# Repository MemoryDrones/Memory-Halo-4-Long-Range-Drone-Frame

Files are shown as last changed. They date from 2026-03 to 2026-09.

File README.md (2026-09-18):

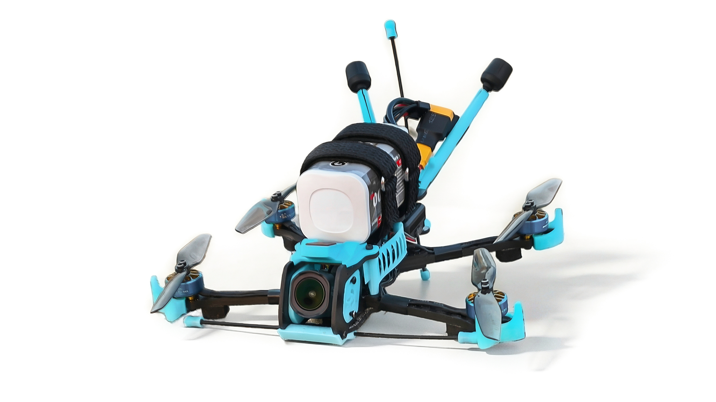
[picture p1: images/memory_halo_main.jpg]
Memory Halo 4 Frame


# Memory Halo 4 Long Range Drone Frame

An open source 4 inch long range FPV drone, designed for those that prefer a stronger frame with less vibrations and no jello. This repository includes DXF carbon cutting files for CNC fabrication and STL files for 3D prints aswell as the hardware and documentation needed for one frame. 

## Features

- 4" Propellor size
- Deadcat configuration
- 0-30 Degree camera angle, nothing obstructs the view, but the camera stays 100% protected!
- Plenty of room inside to fit everything (buzzer, capacitor,...)
- Stack mounting: 20x20mm M3 / 25.5x25.5mm M2 / 25.5x25.5mm M2 (angled 45°)
- Vtx mounting: 20x20mm M2 / 25.5x25.5mm M2
- Motor mounting: 9x9mm and 12x12mm
- Camera support: 19/20mm: Analog, Walksnail, DJI O3 Pro, O4, O4 Pro
- Lightweight: ~205g dry with O4 Pro, ~175g analog
- Supports single or double rear standoff design (seperate middle & top plate design for it)

## Hardware needed
Minimum needed to build the frame. Weight can slightly vary, this is just a guideline.

We have used 20mm standoffs with a diameter of 3.5mm, and a 23mm standoff (for camera plate) with a diameter of 4mm. For any other size, it is possible the TPU files will have to be slightly adjusted.

The frame also uses M2 pressnuts to secure the arms properly in the middle plate.

### Carbon
| Qty | Part name | Details | Weight per piece (g) |
|-----|---|---|---|
| 1 | Bottom plate | Main frame | 5.60 |
| 1 | Middle plate (single standoff or double standoff version) | Main frame | 8.30 / 9.20 |
| 1 | Top plate (single standoff or double standoff version)| Main frame | 8.30 / 9.20 |
| 4 | Arms | Main frame arms | 4.60 |
| 2 | Camera plates | Mounts the camera | 2.10 |

### Standoffs
| Qty | Part name | Details | Weight per piece (g) |
|-----|---|---|---|
| 5 | M2 20mm standoffs | Main spacers | 0.35 |
| 1 | M2 23mm standoff | Spacer for camera plates | 0.40 |

### Screws
| Qty | Part name | Details | Weight per piece (g) |
|-----|---|---|---|
| 4 | M2 14mm screws | Goes through mid plate into standoffs | 0.65 |
| 11 | M2 9mm screws | For everything else | 0.45 |

### Others
| Qty | Part name | Details | Weight per piece (g) |
|-----|---|---|---|
| 4 | M2 pressnuts | Thread inserts for mid plate | 0.45 |
| 2 | Battery pad | Sticky battery pad | 3 |
| 1 | 19/20mm camera mount | TPU camera brackets | 2.2 |

### NOTE: for the "Double rear standoff" version, you need the following extra:
| Qty | Part name | Details | Weight per piece (g) |
|-----|---|---|---|
| 1 | M2 20mm standoffs | Spacer for plate separation | 0.35 |
| 2 | M2 9mm screws | General fasteners | 0.45 |

Total minimum frame weight: ~ 65g

## Repository Content

This repository contains everything needed to cnc cut and build the frame:

- **[/carbon](carbon/)** 
  DXF files for CNC cutting the carbon fiber plates.  
  Includes both **single rear standoff** and **double rear standoff** frame variants (to avoid confusion, please take a look at the readme there).

- **[/3d-prints](3d-prints/)**  
  STL files for TPU printed components such as camera mounts, gps and antenna mounts.

- **[/battery-pad](battery-pad/)**  
  DXF file for laser cutting the battery pad, comes in 2 variations. 

- **[/betaflight-tune](betaflight-tune/)**  
  Betaflight tune specifically for the frame, to get as clean gyro data as possible. indludes screenshots and the cli txt file

- **[/docs](docs/)** 
  Documentation including:
  - Assembly instructions
  [Assembly instructions](docs/assembly-instructions.md)
  - [Example build configurations](docs/build-examples.md)

- **[/images](images/)** 
  Photos and diagrams of the frame are found here.

## Frame assembly

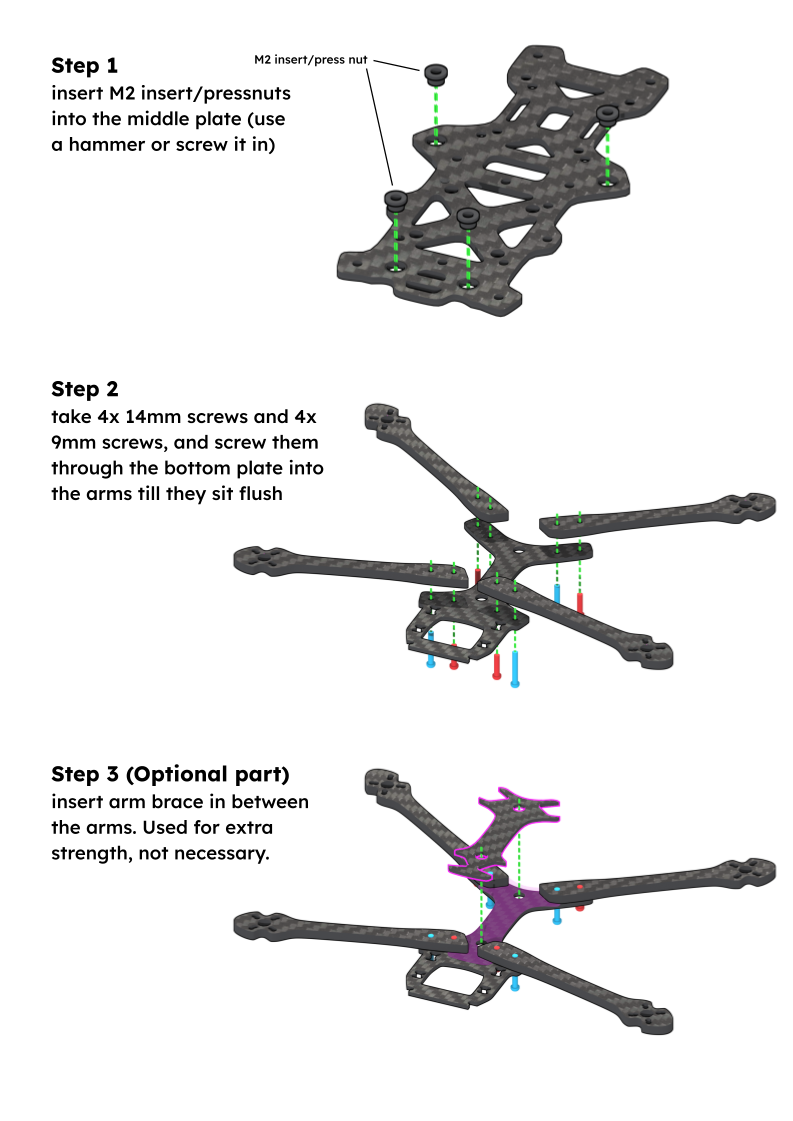
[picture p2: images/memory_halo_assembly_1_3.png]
Memory Halo 4 Frame Assembly Step 1-3


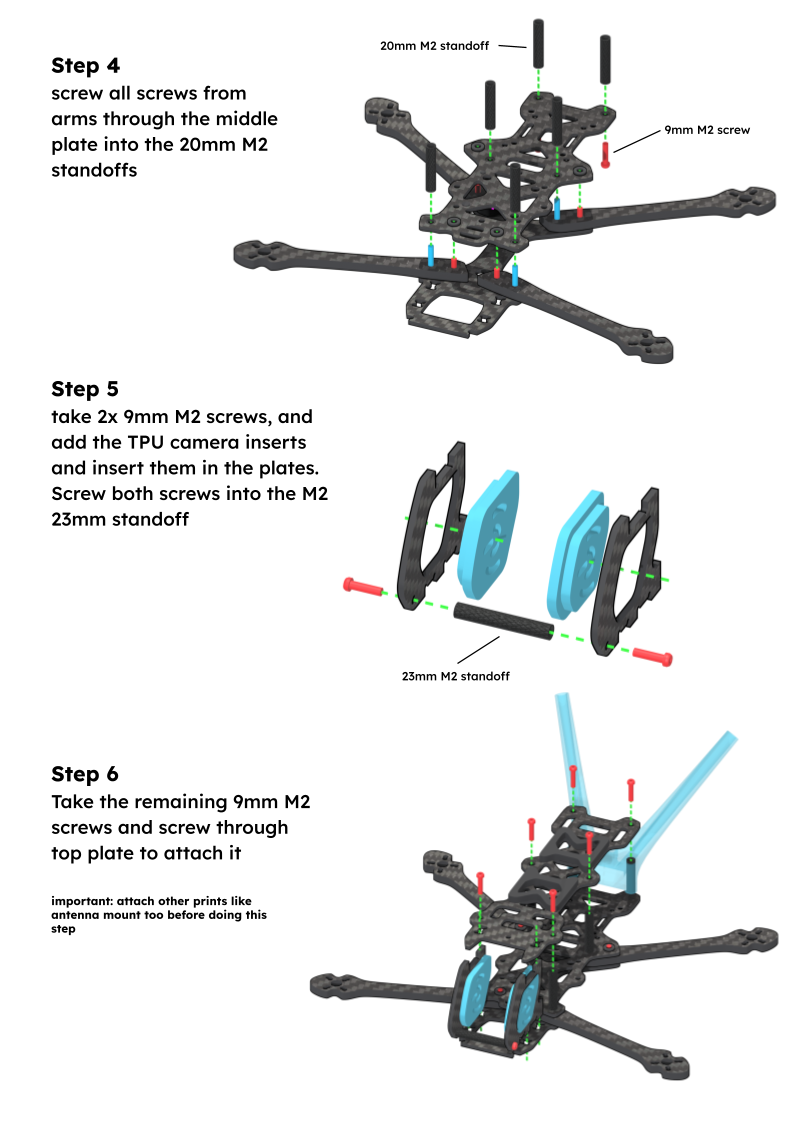
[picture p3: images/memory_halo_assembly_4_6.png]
Memory Halo 4 Frame Assembly Step 4-6


## Photographs of the frame:

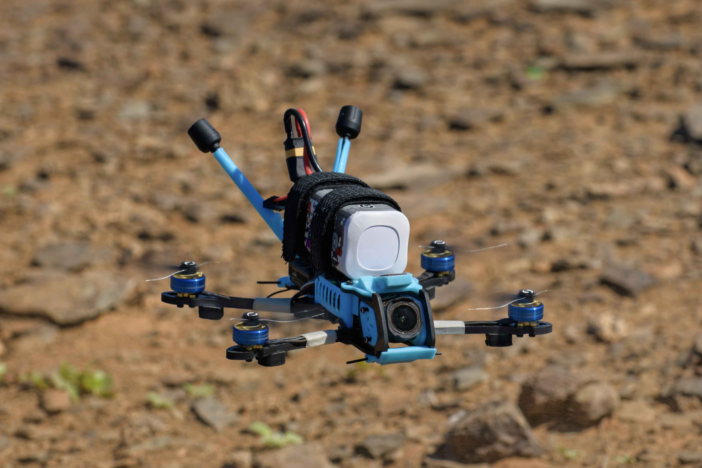
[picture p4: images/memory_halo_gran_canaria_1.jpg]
Memory Halo 4 Gran Canaria 1


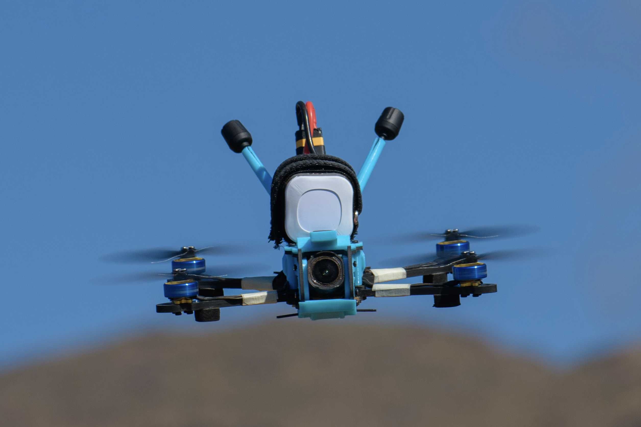
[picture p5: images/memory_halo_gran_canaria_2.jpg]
Memory Halo 4 Gran Canaria 2


## License

This project is licensed under Creative Commons BY-NC 4.0:

- Personal/hobby builds allowed
- CNC shops may cut frames for personal use
- No mass production or commercial selling
- Do not claim as your design

Full license: https://creativecommons.org/licenses/by-nc/4.0/

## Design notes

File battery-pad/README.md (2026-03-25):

## Battery Pad

**Laser-cut sticky battery pad** mounted on the top plate to improve battery grip and reduce vibration.

### Specifications
| Property | Value |
|---|---|
| Quantity | 2 pieces per frame |
| Material | Sticky rubber / foam |
| Thickness | 3mm |

### Variants

Choose one variant and use it for both pieces. Both fit the same top plate.

| Variant 1 | Variant 2 |
|---|---|
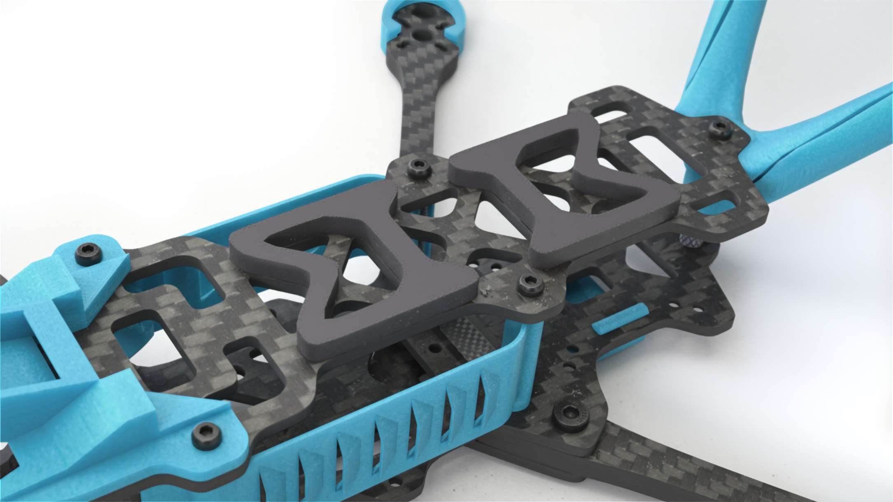
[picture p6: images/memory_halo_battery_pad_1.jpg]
Battery pad variant 1
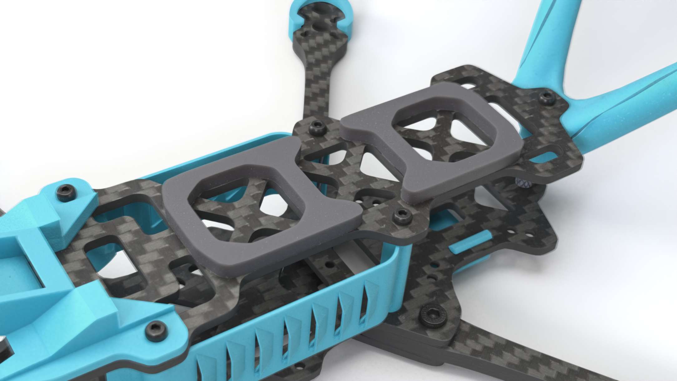
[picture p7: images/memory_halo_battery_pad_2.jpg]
Battery pad variant 2
|  |  |

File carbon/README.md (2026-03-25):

## Carbon Fiber Cutting Files

**Material:** Carbon Fiber (recommended T700)  
**Tolerance:** ±0.05mm ideally

---

## Frame - Shared Parts

| Part | Quantity | Thickness |
|---|-----|---|
| memory_halo_arm_4mm.dxf | 4 | 4mm |
| memory_halo_camera_plate_2mm.dxf | 2 | 2mm |
| memory_halo_bottom_plate_2mm.dxf | 1 | 2mm |
| memory_halo_brace_2mm.dxf* | 1 | 2mm |

*Optional, if you really want the extra strength

---

## Frame Variants

The frame has been made with two variants, one with just a single standoff at the rear, and the second with double standoff. The single standoff saves around 4 grams, but sacrifices a bit on durability and how easy it is to mount parts at the rear.

#### One frame consists of all files in the shared parts folder + & top/mid plate from one variant

### Single Rear Standoff vs Double Rear Standoff
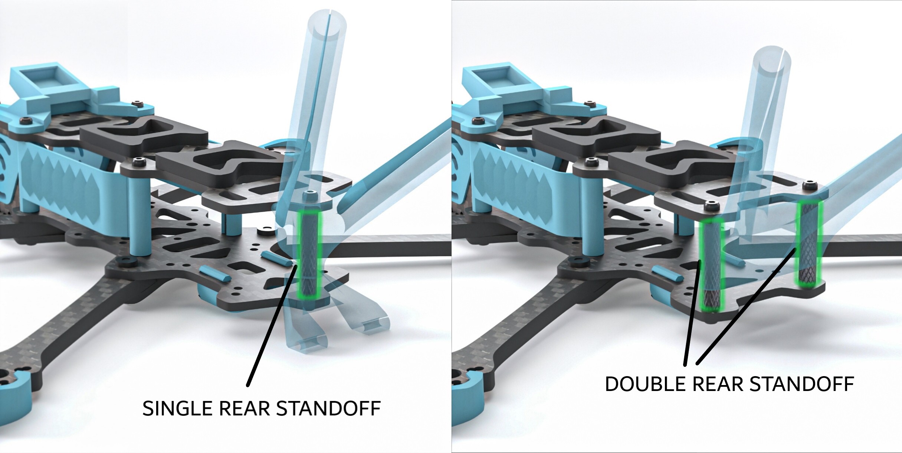
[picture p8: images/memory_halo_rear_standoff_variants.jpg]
Rear standoff variants


### Single Rear Standoff:

| Part | Quantity | Thickness |
|---|-----|---|
| memory_halo_mid_plate_single_standoff_2mm.dxf | 1 | 2mm |
| memory_halo_top_plate_single_standoff_2mm.dxf | 1 | 2mm |

### Double Rear Standoff:

| Part | Quantity | Thickness |
|---|-----|---|
| memory_halo_mid_plate_double_standoff_2mm.dxf | 1 | 2mm |
| memory_halo_top_plate_double_standoff_2mm.dxf | 1 | 2mm |

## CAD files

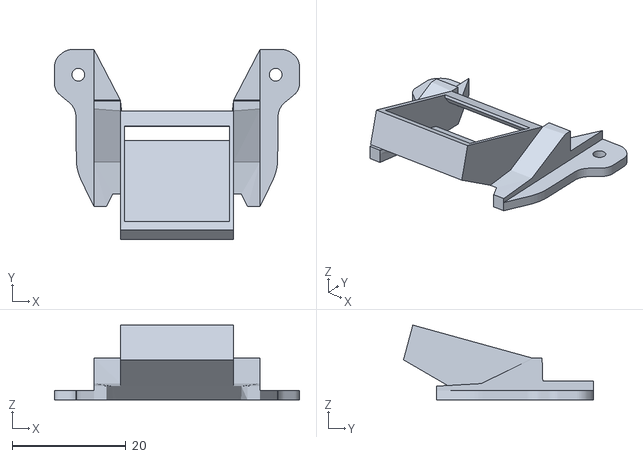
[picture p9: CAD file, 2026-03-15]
3d-prints/memory_halo_goku_mini_v3_gps_mount.stl
43.1 x 33.4 x 13.2

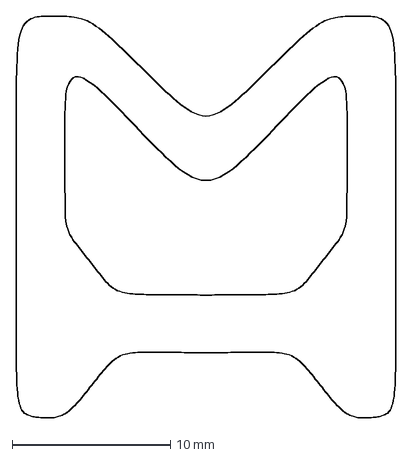
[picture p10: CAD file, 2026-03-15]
battery-pad/memory_halo_battery_pad_1.dxf
24.0 x 25.4 mm

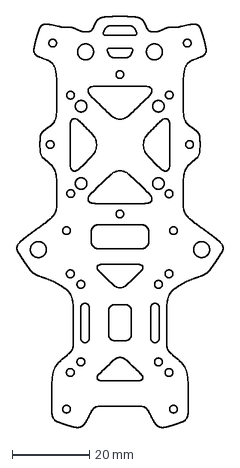
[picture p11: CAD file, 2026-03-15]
carbon/double-rear-standoff/memory_halo_mid_plate_double_standoff_2mm.dxf
53.4 x 106.4 mm

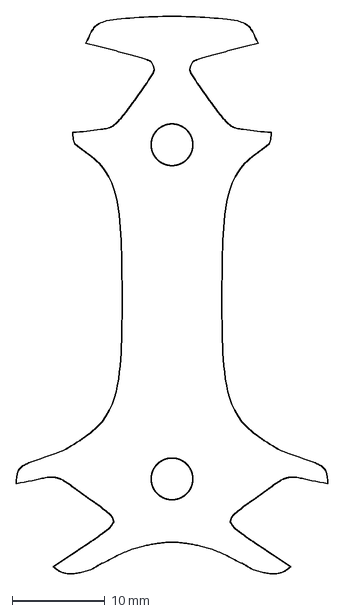
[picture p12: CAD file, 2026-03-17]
carbon/shared-parts/memory_halo_brace_2mm.dxf
33.6 x 60.2 mm

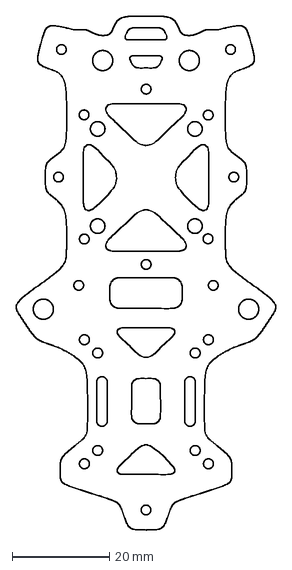
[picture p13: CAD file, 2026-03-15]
carbon/single-rear-standoff/memory_halo_mid_plate_single_standoff_2mm.dxf
53.4 x 105.7 mm

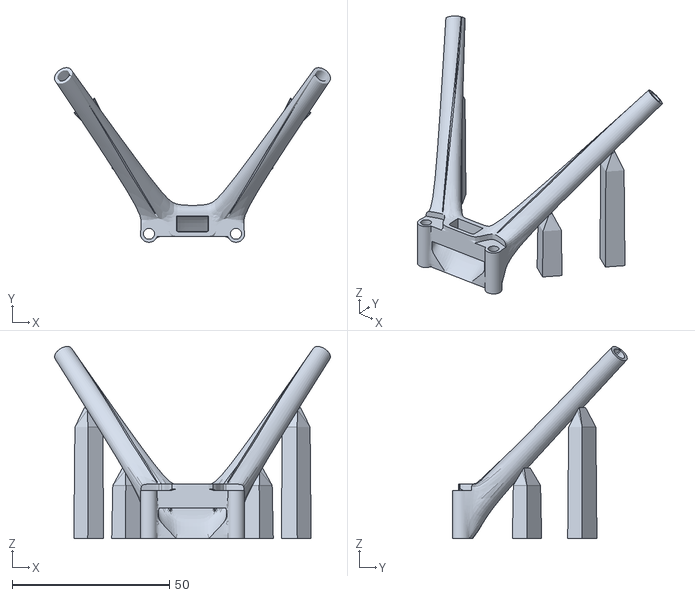
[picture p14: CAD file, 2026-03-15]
3d-prints/memory_halo_1_o4_pro_antenna_xt30_mount.stl
87.7 x 55.5 x 61.0

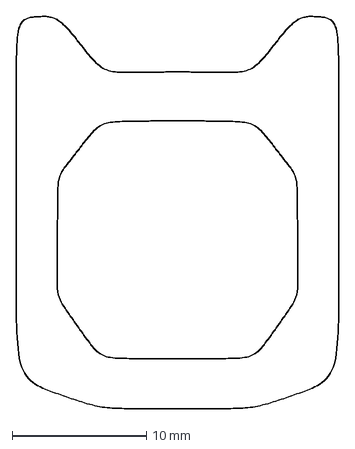
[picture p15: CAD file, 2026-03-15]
battery-pad/memory_halo_battery_pad_2.dxf
24.0 x 29.2 mm

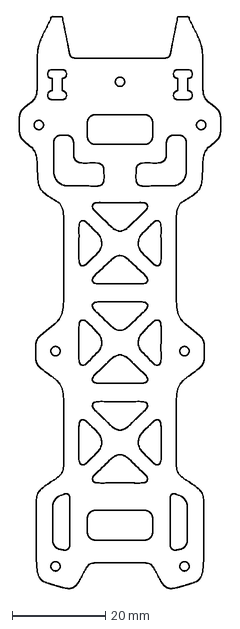
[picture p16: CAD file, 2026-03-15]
carbon/double-rear-standoff/memory_halo_top_plate_double_standoff_2mm.dxf
43.2 x 122.8 mm

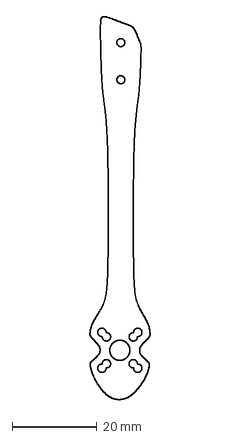
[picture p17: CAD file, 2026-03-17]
carbon/shared-parts/memory_halo_arm_4mm.dxf
14.2 x 90.7 mm

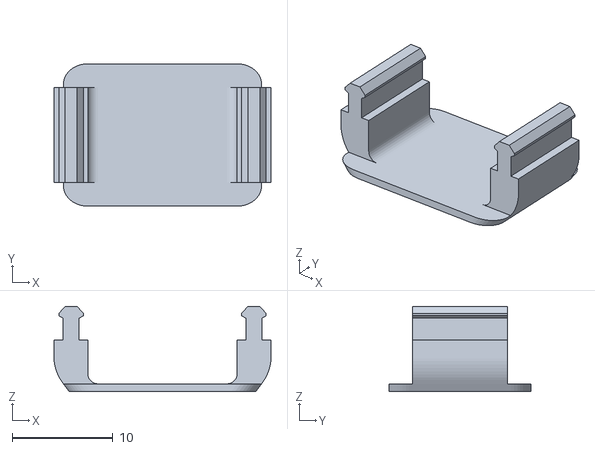
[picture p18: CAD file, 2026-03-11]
3d-prints/memory_halo_bottom_reciever_mount.stl
21.5 x 14.1 x 8.46

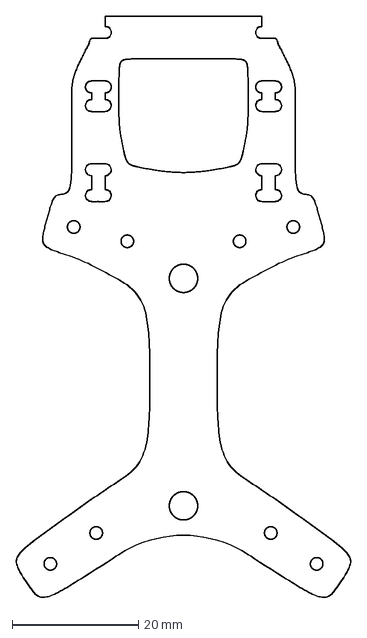
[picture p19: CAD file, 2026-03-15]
carbon/shared-parts/memory_halo_bottom_plate_2mm.dxf
53.0 x 92.2 mm

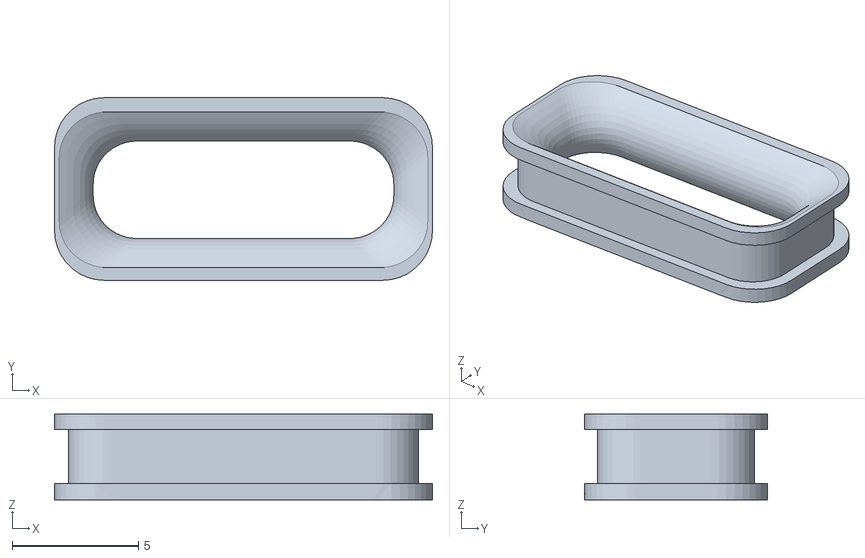
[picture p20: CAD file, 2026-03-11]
3d-prints/memory_halo_xt30_mount_2.stl
14.9 x 7.22 x 3.39

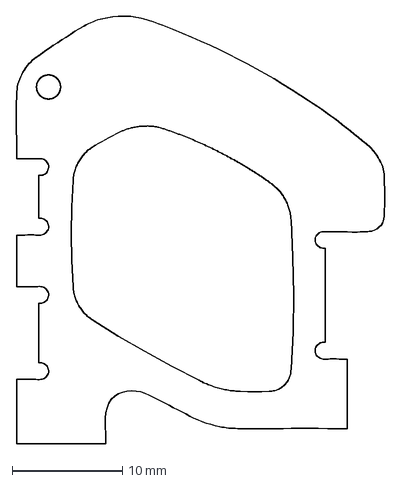
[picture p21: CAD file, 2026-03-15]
carbon/shared-parts/memroy_halo_camera_plate_2mm.dxf
33.5 x 38.9 mm

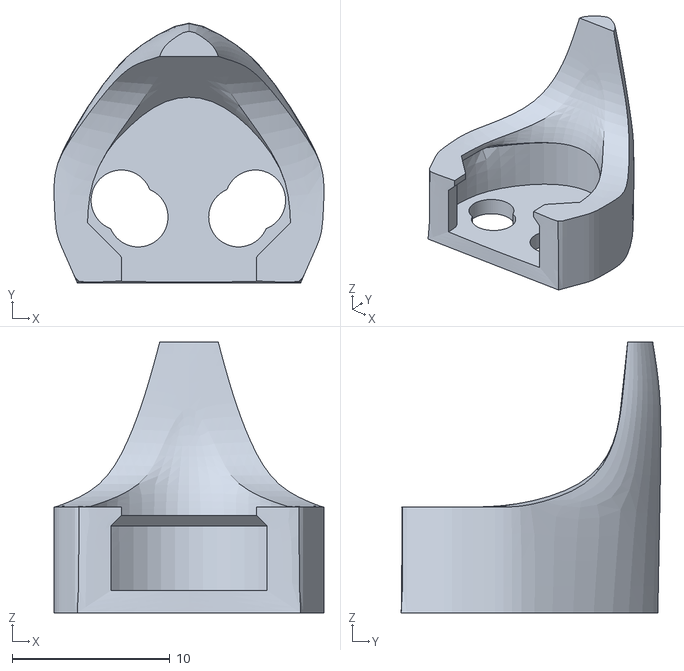
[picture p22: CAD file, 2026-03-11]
3d-prints/memory_halo_rear_protective_arm_mount.stl
17.1 x 16.5 x 17.2

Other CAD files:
3d-prints/memory_halo_protective_cam_mount_19mm.stl
3d-prints/memory_halo_rear_bottom_elrs_antenna_mount.stl
3d-prints/memory_halo_bottom_reciever_mount_large.stl
3d-prints/memory_halo_2_dji_o4_pro_double_antenna_mount_M3.5.stl
3d-prints/memory_halo_arm_motor_mount.stl
3d-prints/memory_halo_bumper.stl
3d-prints/memory_halo_bumper_elrs_antenna_mount.stl
3d-prints/memory_halo_default_cam_mount_19mm.stl
3d-prints/memory_halo_default_cam_mount_20mm.stl
3d-prints/memory_halo_flyfish_gps_mount.stl
3d-prints/memory_halo_front_left_arm_protective_mount.stl
3d-prints/memory_halo_front_right_arm_protective_mount.stl
3d-prints/memory_halo_left_sideplate.stl
3d-prints/memory_halo_protective_cam_mount_20mm.stl
3d-prints/memory_halo_rear_bottom_elrs_antenna_mount_2.stl
3d-prints/memory_halo_right_sideplate.stl
3d-prints/memory_halo_single_antenna_mount.stl
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

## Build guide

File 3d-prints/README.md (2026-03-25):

## 3D Printed Parts

**Material:** TPU  
**Nozzle Temperature:** 205°C  
**Print Speed:** Default settings (20-30 mm/s recommended)

---

## Print Orientation

### Print by Object (Default)
All files should be printed **by object** for a clean aesthetic finish.

Includes: sideplates, camera mounts, antenna mounts, GPS mounts, etc.

### Print by Layer (Exceptions)
These files must be printed **by layer** to ensure proper fit and strength:

- `*_protective_arm_mount.stl`
- `*_arm_motor_mount.stl`
- `*_sma_antenna_mount.stl`

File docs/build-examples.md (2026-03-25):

## Typical 4" Long Range Build

- Motors: 1404 2700–3000kv
- FC/ESC: 25.5x25.5 AIO (30–40A) / 20x20 stack (30A+)
- Battery: 4S 2500–5000mAh Li-ion (200-310g)
- Propellers: 4" 2-blade props
- Receiver: ExpressLRS dual antenna (2.4GHz)
- Video System: Analog, Walksnail, DJI O3 / O4 supported
- VTX: 800mW 20x20 mounting
- Antenna: Long

---

## Example Builds

### Budget Analog Long Range Build (~170g dry)

**Motors**: Skystars Koko 1404 3000kv

**FC/ESC**: SpeedyBee F405 AIO 40A Bluejay

**Camera**: Cadxx Ratel 2

**VTX**: Rush tank ultimate mini VTX

**Antenna**: Singularity 5.8 - SMA LONG Antenna - RHCP By TrueRC

**Receiver**: Happymodel EP1 Dual 2.4GHz

**Battery**: GNB 2500mAh 4S Li-ion / Racepow 5000mAh 4S Li-ion

**Propellers**: HQProp Durable T4x2.5 PC

**Buzzer**: VIFLY Finder Mini

### Digital Long Range Build (~200g dry)

**Motors**: Flywoo Nin 1404 V2 2750kv

**FC/ESC**: Diatone F405 Mini stack

**Camera**: O4 Pro

**VTX**: O4 Pro

**Antenna**: O4 Pro antenna

**Receiver**: Radiomaster ELRS 2.4GHz RP3 V2 Nano Dual

**Battery**: 3000mAh 4S1P XT30 Li-ion Battery Pack

**Propellers**: GEMFAN Hurricane 4024 - 1.5mm Shaft

**Buzzer**: VIFLY Finder Mini

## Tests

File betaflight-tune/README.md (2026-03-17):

## Betaflight Tune

This Betaflight tune is optimized for the Memory Halo 4 frame

Tested on **Betaflight 4.5**.

To apply the CLI .txt file:

1. Connect to Betaflight Configurator
2. Open the **CLI**
3. Paste the contents of `memory_halo_4_tune.txt`
4. Press **Enter**
5. Type `save`

Your flight controller will reboot with the tune applied.

In case you want to double check if everything went correctly, or only adjust a few parameters, take a look at the [tune-screenshots](/tune-screenshots) folder

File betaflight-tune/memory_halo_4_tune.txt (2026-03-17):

# Memory Halo 4 Frame Tune
# Tested on Betaflight 4.5

batch start

# ----------------
# Gyro filtering
# ----------------

set simplified_gyro_filter = ON
set simplified_gyro_filter_multiplier = 100

set gyro_lpf1_type = PT1
set gyro_lpf1_static_hz = 0

set gyro_lpf2_type = PT1
set gyro_lpf2_static_hz = 500

set dyn_notch_count = 1
set dyn_notch_q = 600
set dyn_notch_min_hz = 135
set dyn_notch_max_hz = 500

# ----------------
# RPM filtering
# ----------------

set rpm_filter_harmonics = 3
set rpm_filter_weights = 100,100,100
set rpm_filter_q = 500
set rpm_filter_min_hz = 125
set rpm_filter_fade_range_hz = 50
set rpm_filter_lpf_hz = 150

# ----------------
# D-term filtering
# ----------------

set dterm_lpf1_type = PT1
set dterm_lpf1_static_hz = 75
set dterm_lpf1_dyn_min_hz = 70
set dterm_lpf1_dyn_max_hz = 160
set dterm_lpf1_dyn_expo = 7

set dterm_lpf2_type = PT1
set dterm_lpf2_static_hz = 160

# ----------------
# PID tuning
# ----------------

set p_roll = 47
set i_roll = 92
set d_roll = 34
set f_roll = 100

set p_pitch = 46
set i_pitch = 92
set d_pitch = 37
set f_pitch = 99

set p_yaw = 47
set i_yaw = 92
set d_yaw = 0
set f_yaw = 100

# ----------------
# D-max
# ----------------

set d_max_roll = 34
set d_max_pitch = 37
set d_max_gain = 37
set d_max_advance = 20

# ----------------
# Anti gravity
# ----------------

set anti_gravity_gain = 95
set anti_gravity_cutoff_hz = 5
set anti_gravity_p_gain = 100

# ----------------
# I-term
# ----------------

set iterm_relax = RP
set iterm_relax_type = SETPOINT
set iterm_relax_cutoff = 15
set iterm_windup = 80

# ----------------
# Feedforward
# ----------------

set feedforward_smooth_factor = 25
set feedforward_jitter_factor = 11
set feedforward_boost = 15
set feedforward_max_rate_limit = 90

# ----------------
# Throttle
# ----------------

set throttle_boost = 5
set throttle_boost_cutoff = 15

# ----------------
# TPA
# ----------------

set tpa_mode = D
set tpa_rate = 65
set tpa_breakpoint = 1350
set tpa_low_rate = 20
set tpa_low_breakpoint = 1050

# ----------------
# Simplified PIDs
# ----------------

set simplified_pids_mode = RPY
set simplified_master_multiplier = 105
set simplified_i_gain = 110
set simplified_d_gain = 110
set simplified_pi_gain = 100
set simplified_feedforward_gain = 80
set simplified_pitch_d_gain = 95
set simplified_pitch_pi_gain = 95

save

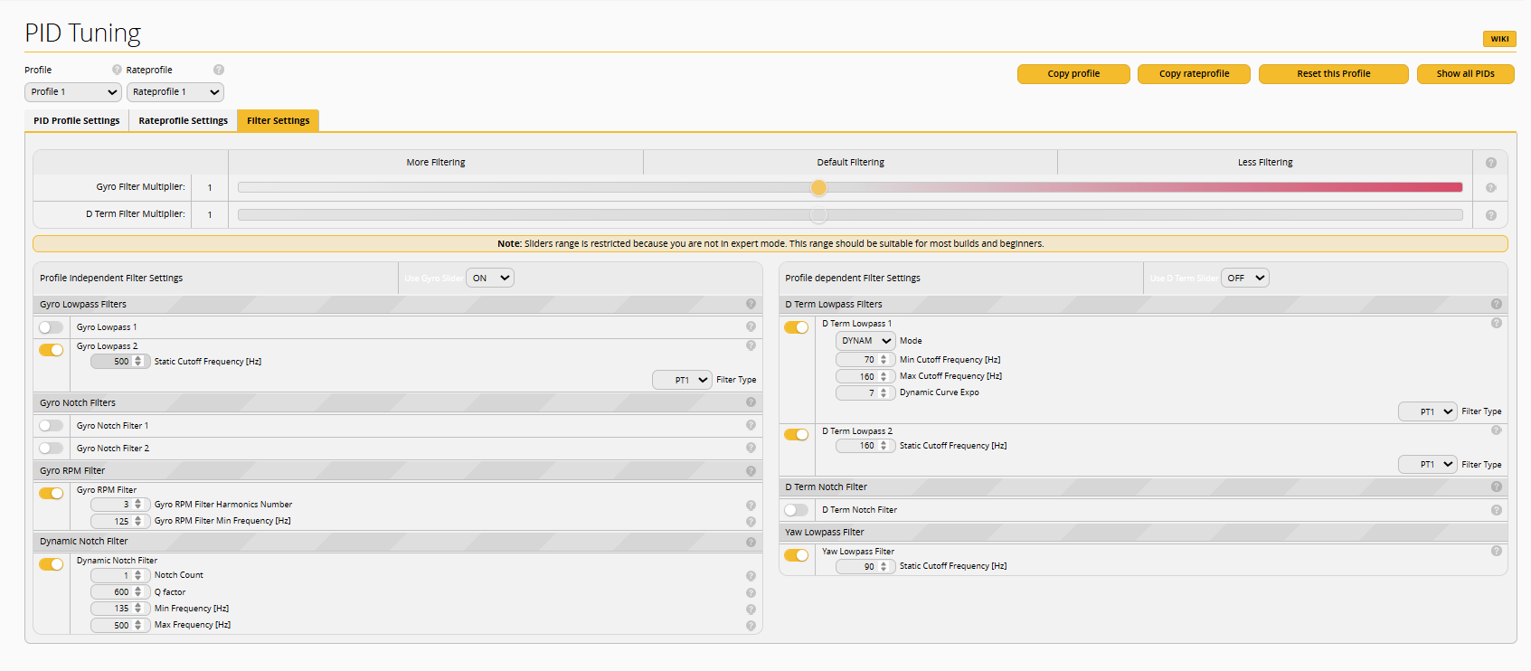
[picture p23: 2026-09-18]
betaflight-tune/tune-screenshots/betaflight-filter-settings.png

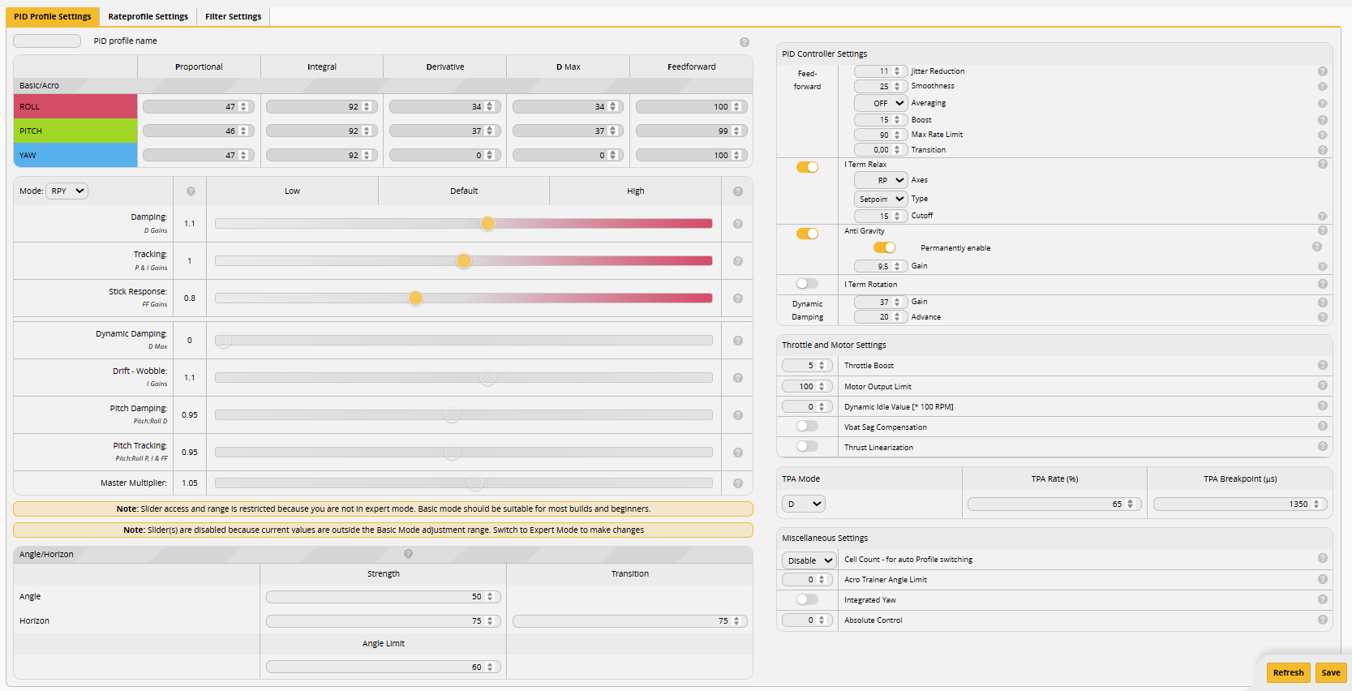
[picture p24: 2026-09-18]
betaflight-tune/tune-screenshots/betaflight-pid-profile.png

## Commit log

2026-03-11 first version of main readme
    [Memory Halo Prints.3mf, memory_halo_bottom_reciever_mount.stl, memory_halo_bottom_reciever_mount_large.stl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]
2026-03-15 added carbon dxf files for both variants, stl 3d printing files and battery pad files
    [memory_halo_1_o4_pro_antenna_xt30_mount.stl, memory_halo_2_dji_o4_pro_double_antenna_mount_M3.5.stl, memory_halo_arm_4mm.dxf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]
2026-03-17 betaflight tune added, frame variation and improved README documentation
    [memory_halo_arm_4mm.dxf, memory_halo_brace_2mm.dxf]
2026-03-25 added assembly instructions and basic readme for the 3d prints + small changes
